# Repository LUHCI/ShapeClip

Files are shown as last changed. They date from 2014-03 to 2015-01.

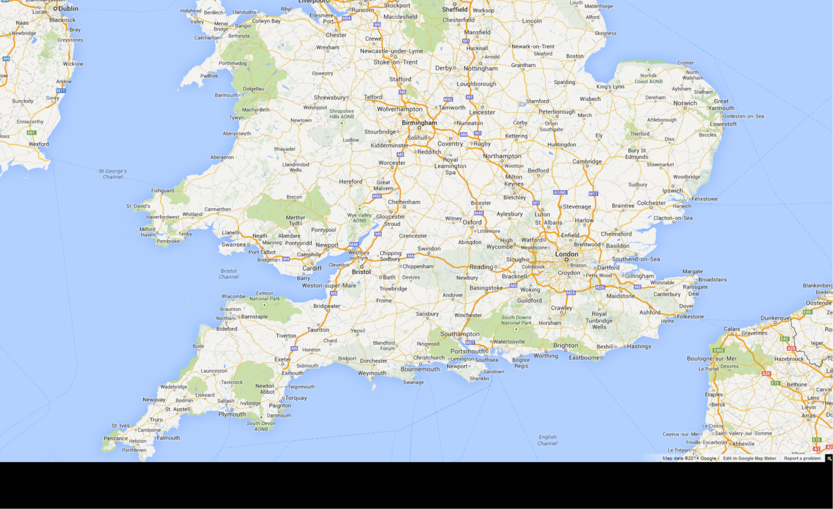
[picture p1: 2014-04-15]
20_Applications/res/uk_map_small.png

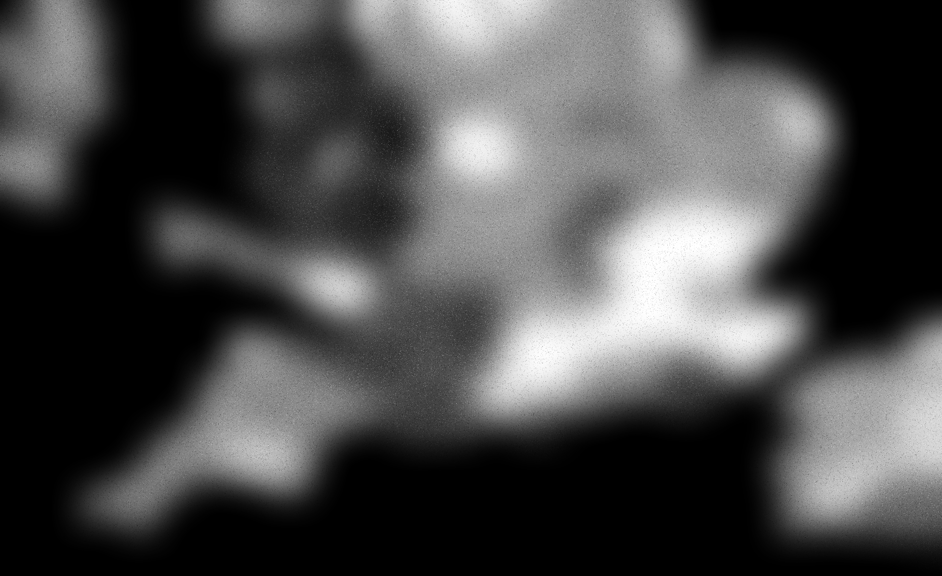
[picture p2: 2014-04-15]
20_Applications/res/uk_population_grayscale.png

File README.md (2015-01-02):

# ShapeClip

## Towards Rapid Prototyping with Shape-Changing Displays for Designers

ShapeClip is a modular tool capable of transforming any computer screen into a z-actuating shape-changing display. This enables designers to produce dynamic physical forms by simply ‘clipping’ actuators onto screens.

ShapeClip displays are portable, scalable, fault-tolerant, and support runtime actuator re-arrangement. Users are not required to have knowledge of electronics or programming, and can develop motion designs with presentation software, image editors, and for those who require more control, web-standard interfaces.

<a href="http://www.youtube.com/watch?feature=player_embedded&v=5YozIqFVEgY
" target="_blank">ShapeClip</a>

## Getting Started

There are 4 main software packages included here:

1. [Clip Firmware](../master/00_Firmware/Firmware/Firmware.ino) + [Servo Extensions](../Slider/00_Firmware/Firmware/Firmware.ino)
2. [Websocket/Serial Bridge](../master/10_Driver/wsserial)
3. [SUR40 Clip Detector (OpenCV)](../master/15_Middleware/ShapeClipDetector)
4. [Javascript API](../master/10_Driver/ShapeClipAPI.js)
5. [Web-based Sample Apps](../master/20_Applications)

In terms of software that can be used to create motion designs, ShapeClip is not restricted to any particular software package. You are free to work with the tools you know.

To get started you will need to get your hands on some ShapeClip hardware.To do that, you can view our design documents in the 01_Hardware folder.

The following image is a trace (from Eagle) of the ShapeClip mkIII board. The different colours denote different layers of the circuit.
ShapeClip mkIII Board

Each standard Clip weighs ≈30g, and is 20×20×80mm when closed, and costs ≈USD$15. The selected stepper motor has 60mm of travel. Under stress, individual Clips draw between 60–540mA at 5V, enabling small groups to be powered via USB. When powering larger numbers, be sure not to make the chain of clips too long as you may damage the Clips. Clips are connected together with pin connectors that double up as a power transmission method. When the Clip is held upright, the top two pins of the power connector are +5v and the bottom one is GND. The motor and circuit logic are kept separate in the top two pins, but in most scenarios they can share power.
ShapeClip mkIII Board

## Research

This work was conducted as part of the GHOST project (http://ghostfet-prod.cs.bris.ac.uk/) to further the understanding of shape-changing computer interfaces.

You can view our paper (CHI2015) online here. To cite the paper, use the following citation: ...

GHOST Logo

## License

Copyright (c) Lancaster University, GHOST Project

Permission is hereby granted, free of charge, to any person obtaining a copy of this software and associated documentation files (the "Software"), to deal in the Software without restriction, including without limitation the rights to use, copy, modify, merge, publish, distribute, sublicense, and/or sell copies of the Software, and to permit persons to whom the Software is furnished to do so, subject to the following conditions:

The above copyright notice and this permission notice shall be included in all copies or substantial portions of the Software.

THE SOFTWARE IS PROVIDED "AS IS", WITHOUT WARRANTY OF ANY KIND, EXPRESS OR IMPLIED, INCLUDING BUT NOT LIMITED TO THE WARRANTIES OF MERCHANTABILITY, FITNESS FOR A PARTICULAR PURPOSE AND NONINFRINGEMENT. IN NO EVENT SHALL THE AUTHORS OR COPYRIGHT HOLDERS BE LIABLE FOR ANY CLAIM, DAMAGES OR OTHER LIABILITY, WHETHER IN AN ACTION OF CONTRACT, TORT OR OTHERWISE, ARISING FROM, OUT OF OR IN CONNECTION WITH THE SOFTWARE OR THE USE OR OTHER DEALINGS IN THE SOFTWARE.

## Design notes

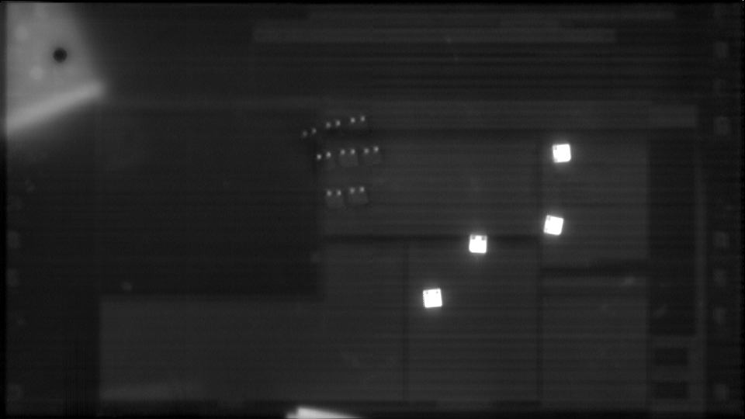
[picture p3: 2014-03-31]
15_Middleware/ShapeClipDetector/ExampleImages/camera635316341878029419.png

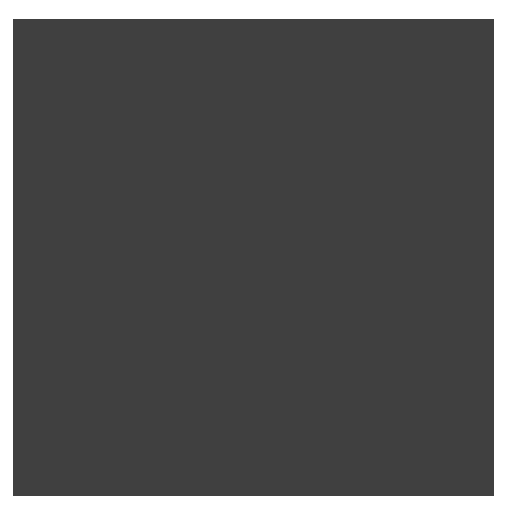
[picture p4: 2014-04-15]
20_Applications/res/lens.png

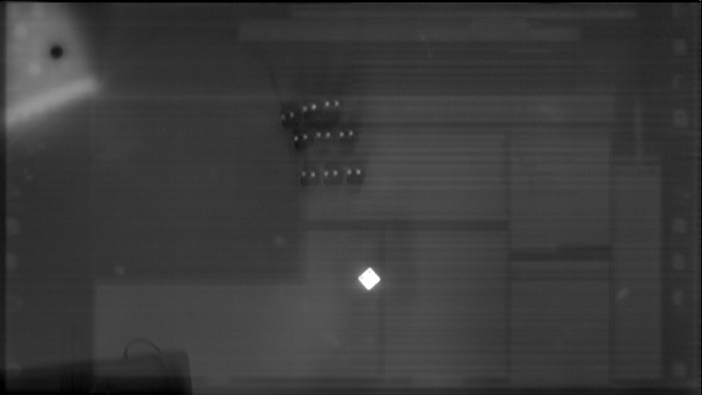
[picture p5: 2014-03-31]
15_Middleware/ShapeClipDetector/ExampleImages/camera635316160988762182.png

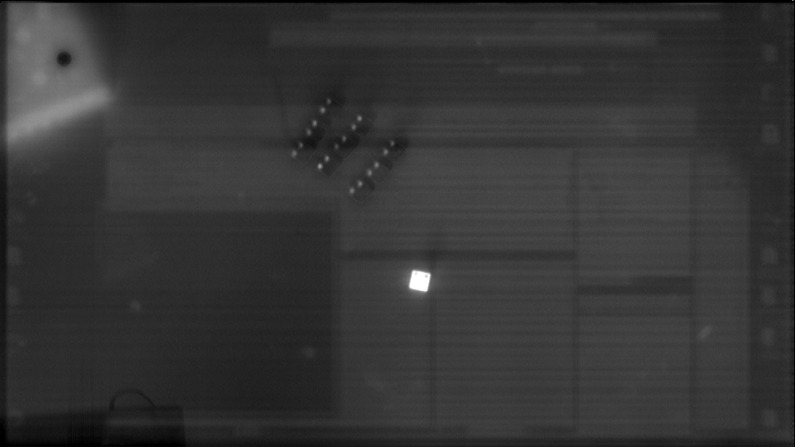
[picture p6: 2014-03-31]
15_Middleware/ShapeClipDetector/ExampleImages/camera635316013497396158.png

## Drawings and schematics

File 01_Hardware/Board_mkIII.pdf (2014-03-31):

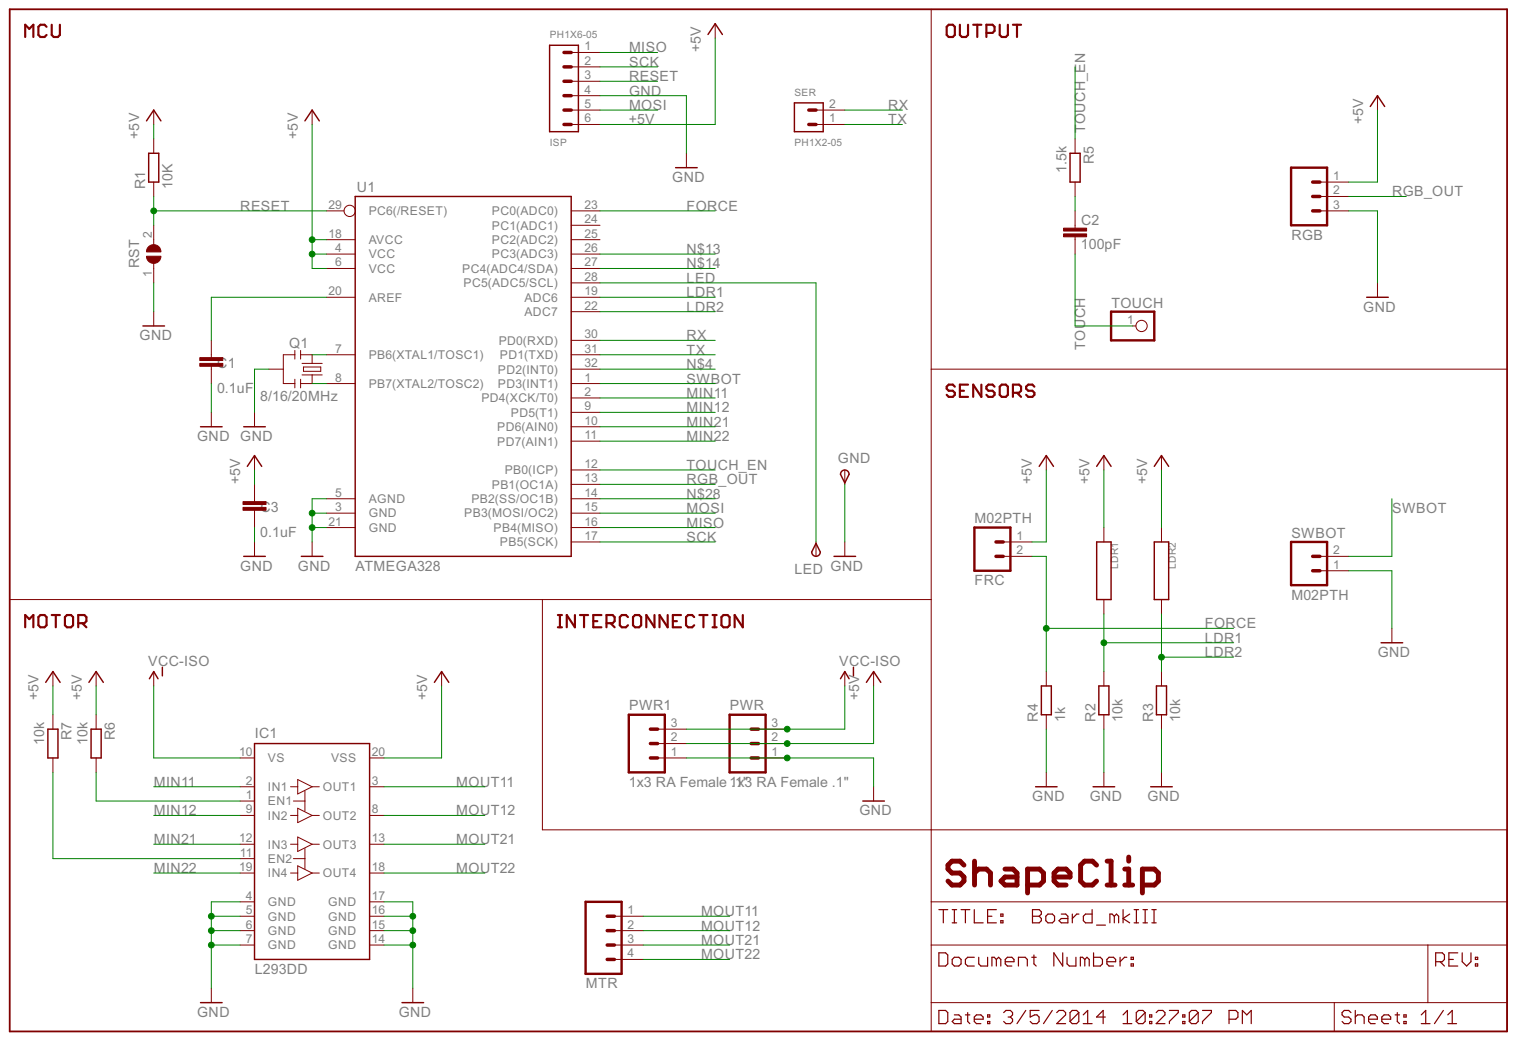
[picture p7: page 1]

VCC-ISO | VCC-ISO

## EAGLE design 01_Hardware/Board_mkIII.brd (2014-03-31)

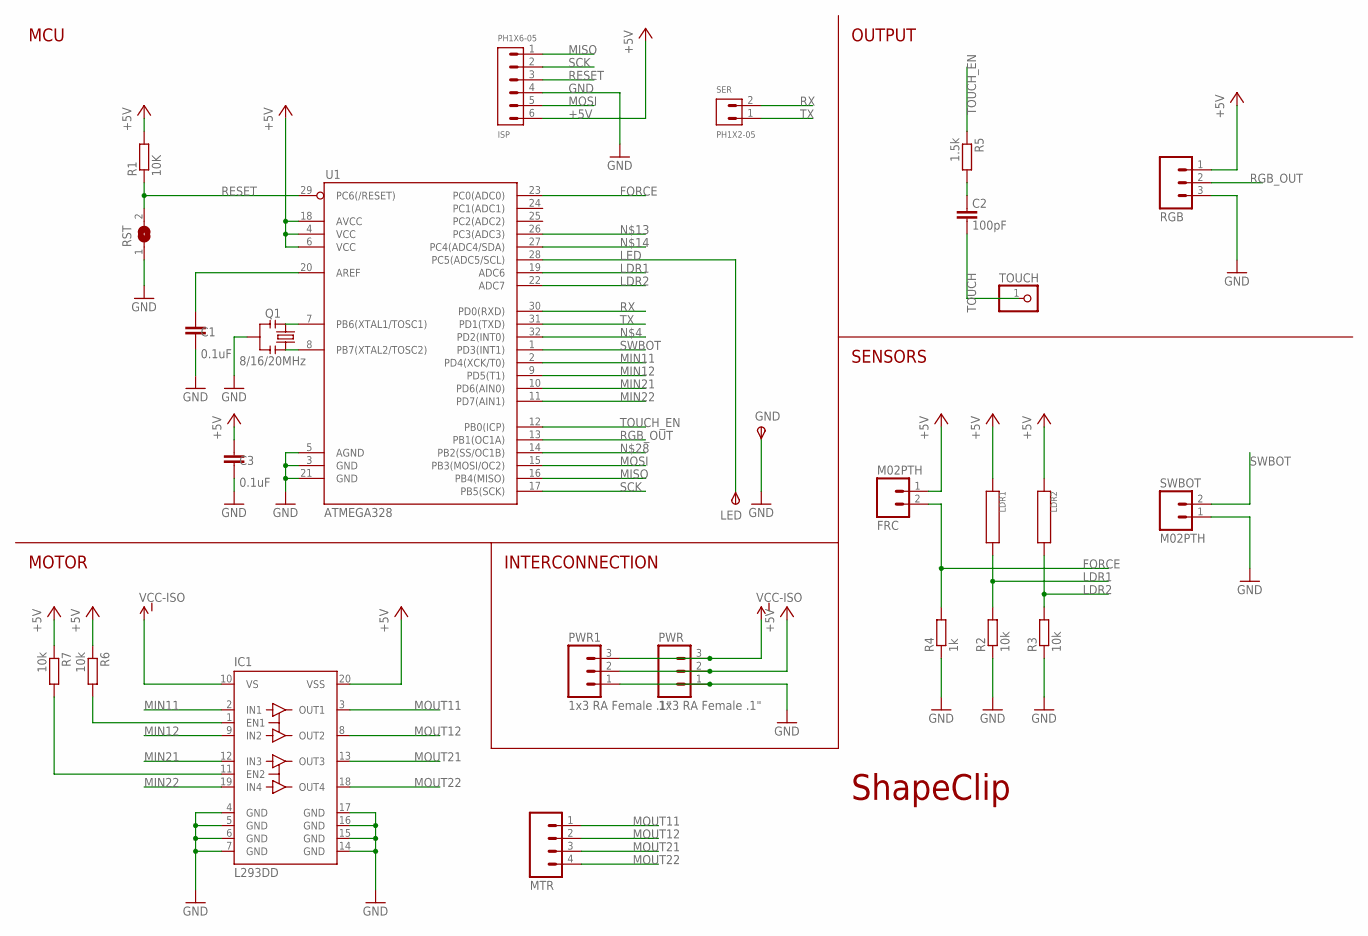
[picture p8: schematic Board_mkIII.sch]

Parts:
C1, C3: 0.1uF; C0603
C2: 100pF; C0603
FRC: M02PTH; 1X02
GND: TPSTP20SQ; TP20SQ
IC1: L293DD; SO20
ISP: PH1X6-05; PH005-1-6
LDR1, LDR2: DR3-31-LDRLONG; DR3-31-LDR_L
LED: TPSTP20SQ; TP20SQ
MTR: M04PTH; 1X04
PWR, PWR1: 1x3 RA Female .1"; PHD_FEMALE_3_90DEG
Q1: 8/16/20MHz; RESONATOR-SMD
R1: 10K; R0603
R2, R3, R6, R7: 10k; R0603
R4: 1k; R0603
R5: 1.5k; R0603
RGB: M03PTH; 1X03
RST: SJW
SER: PH1X2-05; PH005-1-2
SWBOT: M02PTH; 1X02
TOUCH: PINHD-1X1; 1X01
U1: ATMEGA328; TQFP32-08

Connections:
+5V: C3.2, FRC.1, IC1.20 (VSS), ISP.6, LDR1.1, LDR2.1, PWR.2, PWR1.2, R1.2, R6.1, R7.1, RGB.1, U1.4 (VCC), U1.6 (VCC), U1.18 (AVCC)
FORCE: FRC.2, R4.2, U1.23 (PC0(ADC0))
GND: C1.1, C3.1, GND.TP, IC1.4 (GND), IC1.5 (GND), IC1.6 (GND), IC1.7 (GND), IC1.14 (GND), IC1.15 (GND), IC1.16 (GND), IC1.17 (GND), ISP.4, PWR.1, PWR1.1, Q1.2, R2.1, R3.1, R4.1, RGB.3, RST.1, SWBOT.1, U1.3 (GND), U1.5 (AGND), U1.21 (GND)
LDR1: LDR1.2, R2.2, U1.19 (ADC6)
LDR2: LDR2.2, R3.2, U1.22 (ADC7)
LED: LED.TP, U1.28 (PC5(ADC5/SCL))
MIN11: IC1.2 (IN1), U1.2 (PD4(XCK/T0))
MIN12: IC1.9 (IN2), U1.9 (PD5(T1))
MIN21: IC1.12 (IN3), U1.10 (PD6(AIN0))
MIN22: IC1.19 (IN4), U1.11 (PD7(AIN1))
MISO: ISP.1, U1.16 (PB4(MISO))
MOSI: ISP.5, U1.15 (PB3(MOSI/OC2))
MOUT11: IC1.3 (OUT1), MTR.1
MOUT12: IC1.8 (OUT2), MTR.2
MOUT21: IC1.13 (OUT3), MTR.3
MOUT22: IC1.18 (OUT4), MTR.4
unnamed: Q1.1, U1.8 (PB7(XTAL2/TOSC2))
unnamed: Q1.3, U1.7 (PB6(XTAL1/TOSC1))
unnamed: C1.2, U1.20 (AREF)
unnamed: C2.2, R5.2
unnamed: IC1.1 (EN1), R6.2
unnamed: IC1.11 (EN2), R7.2
RESET: ISP.3, R1.1, RST.2, U1.29 (PC6(/RESET))
RGB_OUT: RGB.2, U1.13 (PB1(OC1A))
RX: SER.2, U1.30 (PD0(RXD))
SCK: ISP.2, U1.17 (PB5(SCK))
SWBOT: SWBOT.2, U1.1 (PD3(INT1))
TOUCH: C2.1, TOUCH.1
TOUCH_EN: R5.1, U1.12 (PB0(ICP))
TX: SER.1, U1.31 (PD1(TXD))
VCC-ISO: IC1.10 (VS), PWR.3, PWR1.3

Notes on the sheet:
MCU
MOTOR
SENSORS
OUTPUT
INTERCONNECTION
ShapeClip

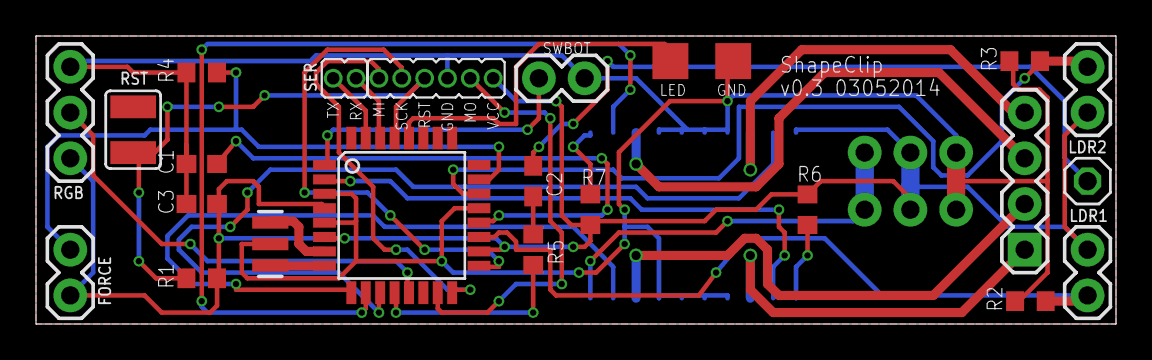
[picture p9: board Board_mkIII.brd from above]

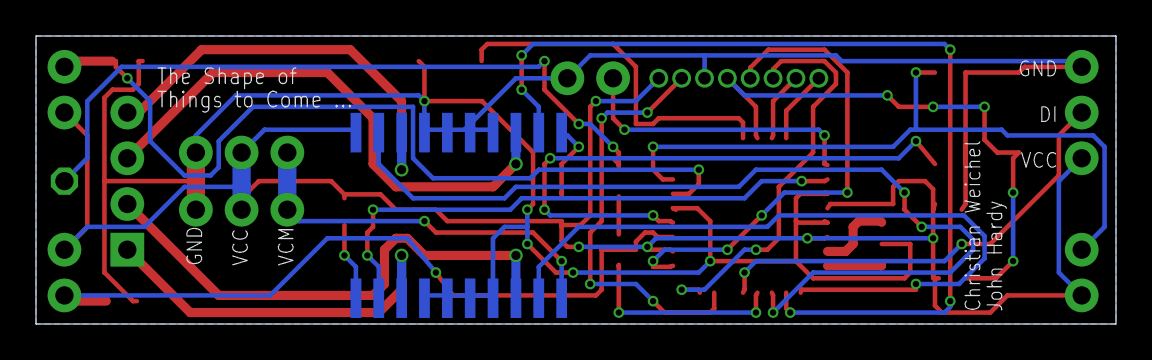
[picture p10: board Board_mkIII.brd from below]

Board: 2 copper layers, 60.0 x 16.0 mm, 27 parts (2 on the bottom side), 31 nets.

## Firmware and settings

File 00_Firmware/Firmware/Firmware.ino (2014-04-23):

/*
	ShapeClip Firmware
	This is logic code used in the ShapeClip paper.
		JH - John Hardy
		CW - Christian Weichel
		JV - John Vidler
		MS - Matthias Schitthelm
	
	v2.5 - JV - Minor tweaks to height mode
	v2.4 - JV - Moved serial buffer updates to a seperate call, serial now updated regardless of mode.	
	v2.3 - JH - Fixes to serial RGB colour display.
	v2.2 - JH - Motor driver accumulator. Known bug which does not let it drive to the extents.
	v2.1 - JH - Bug fixes to the 2.0, added stepper optimisation, decrunchified sync-pulse mode.
	v2.0 - JH - Second version, re-factored and ready for UIST + profiling.
	v1.6 - JV - Updated modes.
	v1.5 - JV - Serial comms added.
	v1.4 - JH - Height mode added.
	v1.3 - JH - Added modes.
	v1.2 - CW - Added LDR.h and LDR.cpp
	v1.1 - CW + MS - Added cool stepper.
	v1.0 - JH - First version, sync-pulse based control of RGB and Height


	/------------------------\
	| SCREEN SERIAL COMMANDS |
 	\------------------------/
        
        Format: [Command][Parameter][X]
        Each part is a single byte, and the last byte should always be ASCII 'X'.
        
        When in serial mode:
        [R][0-255][X] - Set red value
        [G][0-255][X] - Set green value
        [B][0-255][X] - Set blue value
        [H][0-255][X] - Set height value
        [Z][any][X]   - Zero the actuator
        
        When in any mode:
        [M][H][X] - Change to height mode
        [M][Y][X] - Change to syncpulse mode
        [M][S][X] - Change to serial command mode.
        
        
*/

/* External and 3rd party libraries. */ 
#include <Math.h>
#include <EEPROM.h>
#include <util/parity.h>
#include "CoolStepper.h" 
#include "LDR.h"
#include "Adafruit_NeoPixel.h"
#include "WindowVariance.h"

/* IO Pins */
#define PIN_LED   A5		// The on-board LED.
#define PIN_SWTOP 2			// The top switch (digital).
#define PIN_SWBOT 3			// The bottom switch (digital).
#define PIN_FORCE A0		// The force input (analog).
#define PIN_TOUCH 8  		// The touch output (digital).
#define PIN_RGB_OUT 9		// The RGB LED (digital).
#define PIN_MIN11 4			// Motor Coil 1 + (digital).
#define PIN_MIN12 5			// Motor Coil 1 - (digital).
#define PIN_MIN21 6			// Motor Coil 2 + (digital).
#define PIN_MIN22 7			// Motor Coil 2 - (digital).
#define PIN_RND   A4		// Random data source pin.
#define PIN_LDR1  A6		// The LDR1 input (analog).
#define PIN_LDR2  A7		// The LDR2 input (analog).

/* Motor characteristics */
#define MOTOR_ANGLE 20		// The degrees turned with each motor step.
#define MOTOR_SPEED 1500	// The motor speed in rotations per minute (RPMs).
#define MOTOR_TRAVEL 470	// The number of steps to move the nut from the top to the bottom.

/* Sync pulse mode settings. */
const float SYNC_SIGNAL_DROP_THRESHOLD = 3.0f; 				// Based on the behaviour of the LDR with a 10k resistor on a Dell LCD monitor.
const int PULSE_COUNT = 5;									// There are 5 pulses: high, low, r, g, b
const int PULSE_WIDTH = 200;								// The amount of time each pulse last (ms).
const int PULSE_WIDTH_ERR = 10;								// The amount of error in each pulse width start and end (~10ms due to 4ms timers in JS).
const int DATA_WIDTH  = PULSE_WIDTH * PULSE_COUNT;			// The total amount of time for an entire data pulse.
const int DATA_WIDTH_ERR = PULSE_WIDTH_ERR * PULSE_COUNT; 	// The total amount of error for an entire data pulse.
const int SAMPLE_OFFSET = 50;								// The amount of time (ms) to offset the LDR sampling start (relative to the sync drop).
const int SAMPLE_WINDOW = 90;								// The amount of time (ms) to sample the LDR for.

#define PULSE_STATE__NOT_CHECKED  -1	// The sync-pulse routine did not bother checking, too soon since previous check.
#define PULSE_STATE__NO_PULSE      0	// The sync-pulse check returned no pulse.. Probably off a screen.
#define PULSE_STATE__ACTIVE_PULSE  1	// The sync-pulse check returned a pulse! It's probably on a screen.

/** Sensor settings. */
#define ON_SCREEN_TIMEIN 500			// The amount of time before height mode accepts an on screen value. One second in ms.
const int LDR_MIN_LIMIT = 120;				// The smallest acceptable delta between the min and max values of the LDR.
const int LDR_MAX_LIMIT = 1000;				// The largest acceptable delta between the min and max values of the LDR.
#define LDR_OFFSCREEN_DELTA_GAP 100 	// The largest gap between the LDR values at which it is considered off-screen.
#define SSMODE_LDR_SYMB_LOWER -450		// The cap for the lowest LDR symbol.
#define SSMODE_LDR_SYMB_UPPER 500		// The cap for the highest LDR symbol.

/* Application Behaviours */
#define MODE_PROFILING 			// Does the Clip accept basic serial commands: p,s,f (ping, start, finish).
#define PROFILING_RATE 50U		// The rate at which we stream data to serial in profiling mode.
#define SSMODE_8BIT				// Run screen-serial in 8 bit mode (recommended).
//#define SSMODE_16BIT			// Run screen-serial in 16 bit mode (not recommended or tested that much).

/* Serial Debugging modes. */
//#define HEIGHT_DEBUG			// Height mode: Enable serial print of debug messages.
//#define SYNCPULSE_DEBUG		// Sync pulse mode: Enable serial print of debug messages.
//#define SSMODE_CMDPRINT		// Screen serial mode: Enable serial print of command buffer interpretations.
//#define SSMODE_STREAMPRINT	// Screen serial mode: Enable serial print of bitstream data for debugging the serial connection.  <-- this one is cool
//#define SSMODE_TRANSMISSION_GRAPH // Print out the data for the screen-serial transmission graph.
//#define SERIAL_INFO			// Should device values be streamed via serial? csv: ms, ldr1, ldr2, rgb, height, frc, haspulse, swbot
//#define SERIAL_SYNC_DEBUG		// Should sync pulse debug data be streamed via serial? csv: ms, r, g, b
//#define SERIAL_SYNC_DEBUG2	// Should the verbose sync pulse debug data be streamed via serial? csv: ms, slope, max, r, g, b, min, raw
//#define EMIT_MODES

/** Colour modes - how the RGB LED is controlled. */
#define RGBMODE_NONE     0		// The RGB LED displays nothing.
#define RGBMODE_SCREEN   1		// The RGB LED displays the last colour the pulses detected.
#define RGBMODE_NOSCREEN 2		// The RGB LED displays the "not on screen" pattern (i.e. no pulse detected).
#define RGBMODE_STARTUP  3		// The RGB LED displays the "setting up / calibrating" pattern.

/* Colour manipulation macros. */
#define RGB(r,g,b) 	(((r & 0xFF) << 16) | ((g & 0xFF) << 8)  | ((b & 0xFF) << 0))
#define RED(hex) 	hex >> 16 & 0xFF
#define GREEN(hex) 	hex >>  8 & 0xFF
#define BLUE(hex) 	hex >>  0 & 0xFF

/** EEPROM data settings. NOTE: Modes cannot be zero - zero is reserved! */
#define EEMODEADDR 0			// The address of the mode stored in EEPROM.
#define EEMODE_CHANGETIME 5000  // The number of ms to hold the switch before the clip mode is changed.
#define EEMODE_SYNCPULSE  45	// The Clip looks for a sync pulse on one of the LDRs.
#define EEMODE_HEIGHTONLY 37	// The Clip uses both LDRs to estimate height, no colour involved.
#define EEMODE_SERIAL     89	// The Clip can send / recieve serial data with a simple protocol.



/**
 * @brief Check to see if code should be called based on the timer.
 * This can be used to create a rudimentary timer.  It is called once per logic-loop.
 * If it returns true, then the timer handler code should be run.  If false, then it should not.
 * Based on: http://forum.arduino.cc/index.php/topic,5686.0.html
 * Usage: ulong timer = 0; if (cycleCheck(&timer, 10u) { log("called every 10 ms"); }
 * @param *iLastMs Pointer to a value which contains the last time this was checked.
 * @param iCycle The number of ms since the last time required to trigger.
 * @return True if the time since the last call has elasped and the code should run. False if not.
 */
boolean cycleCheck(unsigned long *iLastMs, unsigned int iCycle)  {
	unsigned long ms = millis();
	if(ms - *iLastMs >= iCycle)
	{
		*iLastMs = ms;
		return true;
	}
	else
	{
		return false;
	}
}

/**
 * @brief Reset a timer that is used with the cycleCheck function.
 * @param *iLastMs Pointer to a value which contains the last time this was checked.
 * This will update the iLastMs value to the current time.
 */
void cycleReset(unsigned long *iLastMs) {
	*iLastMs = millis();
}

/**
 * @brief Work out if a time value falls within a sample window. 
 * @param iRelativeTime The time to check.
 * @param iSampleOffset The sampling offset start (relative to 0 in iRelativeTime).
 * @param iWindowSize The sampling window size.
 * @return True if (iSampleOffset+iWindowSize) > iRelativeTime > iSampleOffset.
 */
boolean checkSample(int iRelativeTime, int iSampleOffset, int iWindowSize) {
	return (iRelativeTime > iSampleOffset) && ( iRelativeTime < (iSampleOffset + iWindowSize));
}


// ShapeClip v1 controls and live values.
Stepper motor(MOTOR_ANGLE, PIN_MIN11, PIN_MIN12, PIN_MIN21, PIN_MIN22);
Adafruit_NeoPixel pRGB = Adafruit_NeoPixel(1, PIN_RGB_OUT, NEO_GRB + NEO_KHZ800);
LDR ldr1(PIN_LDR1);
LDR ldr2(PIN_LDR2);

boolean bMotorCalibrated = false;	// Is the motor position value accurate?
int iMotorPosition = 0;				// The current number of steps in the motor.

int eClipMode = EEMODE_SYNCPULSE;	// Current Clip mode.
int eRGBMode = RGBMODE_NONE;		// Current RGB mode.
bool bOnScreen = false;				// Is the shape clip device on the screen (i.e. does it have a valid sync pulse)?

int iTargetR = 0;					// Target RED component.
int iTargetG = 0;					// Target GREEN component.
int iTargetB = 0;					// Target BLUE component.
int iTargetPos = 0;					// Target MOTOR height (steps).



/**
 * @brief Configure the chip pins to the proper states.
 */
void configure() {
	
	// On-board LED (output, off).
	pinMode(PIN_LED, OUTPUT);
	digitalWrite(PIN_LED, LOW);
	
	// LDR1 and LDR2 (input). NOT REQUIRED FOR ANALOG PINS - MAYBE HARMFUL
	//pinMode(PIN_LDR1, INPUT);
	//pinMode(PIN_LDR2, INPUT);
	
	// Top and bottom switches (input, active).
	pinMode(PIN_SWTOP, INPUT);
	digitalWrite(PIN_SWTOP, HIGH);
	pinMode(PIN_SWBOT, INPUT);
	digitalWrite(PIN_SWBOT, HIGH);
	
	// Touch sensor (output, low).
	pinMode(PIN_TOUCH, OUTPUT);
	digitalWrite(PIN_TOUCH, LOW);
	
	// Force sensor (input).
	pinMode(PIN_FORCE, INPUT);
	
	// Set up the motor.
	motor.setSpeed(MOTOR_SPEED);
	
	// Set up the RGB LED.
	pRGB.begin();
	pRGB.show();
	
	// On-board LED (on).
	digitalWrite(PIN_LED, HIGH);
}

/**
 * @brief This will send the motor DOWN until the SWBOT is triggered OR the full MOTOR_TRAVEL is used.
 * It will set the iMotorPosition value to 0 and not allow calls to moveMotor while operating.
 */
void zeroMotor() {
	
	// Zero flags.
	bMotorCalibrated = false;
	
	// Put us into setup mode (RGB LED).
	int eLastMode = eRGBMode;
	eRGBMode = RGBMODE_STARTUP;
	updateColour();
	
	// Until the motor is calibrated, step down each time.
	for(int iAvailableSteps = MOTOR_TRAVEL; iAvailableSteps >= 0; iAvailableSteps--) {
		motor.step(-1);

		//#ifdef SWBOT_MOTOR
		//if (digitalRead(PIN_SWBOT) == LOW) break;
		//#endif
	}
	
	// Set the motor position to 0 (known location).
	bMotorCalibrated = true;
	iMotorPosition = 0;
	
	// Shut the motor down.
	motor.shutdown();
	
	// Take us out of setup mode.
	eRGBMode = eLastMode;
	updateColour();
}


/**
 * @brief Move the motor one step towards the target position.
 * TODO: There is currently an edge case where we cannot drive the motor all the way to the top.
 */
void moveMotor() {
	
	// Only do this if the motor is calibrated.
	if (!bMotorCalibrated)
		return;
	
	#define STEP_ACCM_SIZE 5								// The max number of steps to accumulate before batching.
	static boolean bAllowMotorShutdown = true;				// Is the motor allowed to shutdown.
	static unsigned long shutdownTimeout = millis();		// The time of the last step.
	static unsigned int iStepAccumulator = 0;				// The step accumulator.
	
	
	// If we have a small change in position, add it to the accumulator.
	//   so that we can batch it later.  If we do not do this, small steps
	//   are often lost.
	//   This also has the nice side effect as acting like a noise absorber.
	int iDelta = iTargetPos - iMotorPosition;
	if (abs(iDelta) < STEP_ACCM_SIZE)
	{
		iStepAccumulator += iDelta;
		iDelta = 0;
	}
	
	// If the accumulated steps + the change this frame is over the minimum step, then step.
	int iAdjustedSteps = iStepAccumulator + iDelta;
	
	// Or if we are at either end (the accumulator would absorb it, so we need a (literal) edge case).
	//bool bEdgeCase = ((iTargetPos < (0 + STEP_ACCM_SIZE)) || (iTargetPos > (MOTOR_TRAVEL - STEP_ACCM_SIZE)) & abs(iAdjustedSteps) > 2) ;
	
	// Do the check.
	if (abs(iAdjustedSteps) >= STEP_ACCM_SIZE /* || bEdgeCase */) 
	{
		// Compute the step direction.
		int step = iAdjustedSteps >= 0 ? 1 : -1;
		
		/* vv This approach leads to jumpy / inconsistent step behaviours.
		// Limit to 25 steps per frame.
		if (abs(iAdjustedSteps) <= 25)
		{
			motor.step(step * iAdjustedSteps);
			iMotorPosition += (step * iAdjustedSteps);
		}
		else
		{
			motor.step(step * 25);
			iMotorPosition += (step * 25);
		}
		*/
		
		/* vv This approach leads to faster and smoother stepping, kinda tearing noisy tho. */
		if (abs(iAdjustedSteps) > 20)
		{
			motor.step(step * 20);
			iMotorPosition += (step * 20);
		}
		if (abs(iAdjustedSteps) > 10)
		{
			motor.step(step * 10);
			iMotorPosition += (step * 10);
		}
		else
		{
			motor.step(step);
			iMotorPosition += step;
		}
		
		//Serial.print("Stepping ");
		//Serial.println(iAdjustedSteps);
		
		// Write the last step time.
		shutdownTimeout = millis();
		bAllowMotorShutdown = true;
	}
	
	// If we have not stepped for 0.5s, turn off the motor.
	if ((millis() - shutdownTimeout) > 250)
	{
		// If we have not already shut the motor down.
		//if (bAllowMotorShutdown)
		//{
			motor.shutdown();
			bAllowMotorShutdown = false;
		//}
	}
	
	
	
	
	/*
	// Compute the distance to travel.
	int iDelta = iTargetPos - iMotorPosition;
	
	// If we have to move over 2 steps in either direction.
	if (abs(iDelta) > 1)
	{
		// Move one step in the correct direction and update the motor position.
		int step = iDelta >= 0 ? 1 : -1;
		
		// Skip for 20 steps.
		if (abs(iDelta) > 20)
		{
			motor.step(step * 20);
			iMotorPosition += (step * 20);
		}
		// Skip for 10 steps.
		if (abs(iDelta) > 10)
		{
			motor.step(step * 10);
			iMotorPosition += (step * 10);
		}
		// Detailed steps.
		else
		{
			motor.step(step);
			iMotorPosition += step;
		}
	}
	
	// Otherwise shut the motor down.
	else
	{
		motor.shutdown();
	}
	*/
}

/**
 * @brief Display the correct colour on the RGB led based on the mode it is in.
 */
void updateColour() {
	
	// If we are in the normal mode.
	switch (eRGBMode)
	{
		case RGBMODE_NONE:
			pRGB.setPixelColor(0,  0, 0, 0);
			break;
		case RGBMODE_SCREEN:
			{
				// Go immediately to the new colour.
				// pRGB.setPixelColor(0,  iTargetR, iTargetG, iTargetB);
				
				// Get 1% closer to the target colour each iteration.
				uint32_t currentColor = pRGB.getPixelColor(0);
				int stepRed   = constrain(map(10, 0, 1000, RED(currentColor),   iTargetR), 0, iTargetR);
				int stepGreen = constrain(map(10, 0, 1000, GREEN(currentColor), iTargetG), 0, iTargetG);
				int stepBlue  = constrain(map(10, 0, 1000, BLUE(currentColor),  iTargetB), 0, iTargetB);
				
				// Set the step value.
				pRGB.setPixelColor(0,  stepRed, stepGreen, stepBlue);
			}
			break;
		case RGBMODE_NOSCREEN:
			pRGB.setPixelColor(0,  255, 0, 0);
			break;
		case RGBMODE_STARTUP:
			if (eClipMode == EEMODE_HEIGHTONLY)
				pRGB.setPixelColor(0,  255, 0, 0);
			else if (eClipMode == EEMODE_SYNCPULSE)
				pRGB.setPixelColor(0,  0, 255, 0);
			else
				pRGB.setPixelColor(0,  0, 0, 255);
			break;
	}
	
	// Push the new colour.
	pRGB.show();
}




/**
 * Setup the board and configure the pins.
 */
void setup() { 
	
	// Configure the board and pins.
	configure();
	
	// Start the serial port.
	Serial.begin(115200);
	
	// Wait two seconds.
	Serial.println("Boot v2.5");
	
	// Select a default clip mode from the set of possible modes, if one is not set.
	eClipMode = EEPROM.read(EEMODEADDR);
	switch( eClipMode )
	{
	  case EEMODE_SYNCPULSE:
		break;
	  case EEMODE_HEIGHTONLY:
		break;
	  case EEMODE_SERIAL:
		break;
	  default:
		eClipMode = EEMODE_HEIGHTONLY;
		EEPROM.write(EEMODEADDR, EEMODE_HEIGHTONLY);
	}

	// Debug Mode
	//eClipMode = EEMODE_SYNCPULSE;
	//eRGBMode  = RGBMODE_SCREEN;
	detectAndSetModeChange( -1 );   // -1 == set nothing, blink code; 0 = set nothing, wait for button; >0 == set mode to supplied mode

	// Wait for a random time so that not all clips zero their motor at the same time.
	randomSeed(analogRead(PIN_RND));
	uint16_t randomWait = random(1000);
	delay(randomWait);
	
	// Bring the motor down until it hits the bottom.
	zeroMotor();
	
	// make sure we all start at the same time
	delay(1000 - randomWait);
}
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
void loop() {
	
	// Listen for a change in mode.
	detectAndSetModeChange( 0 );

	// Attempt to read a serial bit from the screen.
	screenSerialRead();
	if( cmdBuffer[0] == 'M' && cmdBuffer[2] == 'X' )
	{
		switch( cmdBuffer[1] )
		{
			case 'H': detectAndSetModeChange( EEMODE_HEIGHTONLY ); break;
			case 'Y': detectAndSetModeChange( EEMODE_SYNCPULSE ); break;
			case 'S': detectAndSetModeChange( EEMODE_SERIAL ); break;
		}
		cmdBuffer[0] = 0;
		cmdBuffer[1] = 0;
		cmdBuffer[2] = 0;
	}
	
	// Detect which mode we are in.
	switch (eClipMode)
	{
		// If we are in EEMODE_HEIGHTONLY mode, just use both LDRs for height.
		case EEMODE_HEIGHTONLY:
			loopHeightMode();
			break;
			
		// If we are in EEMODE_SYNCPULSE mode, use the height and colour.
		case EEMODE_SYNCPULSE:
			loopSyncPulseMode();
			break;
			
		// If we are in EEMODE_SERIAL, use the simple binary protocol.
		case EEMODE_SERIAL:
			loopSerialMode();
			break;
			
		// Unknown mode.. should not get here.
		default:
			break;
	}
	
	// If we are in profiling mode.
	#ifdef MODE_PROFILING
	
	static bool bMeasuring = false;			// Are we measuring.
	static unsigned int iMeasureCount = 0;	// How many have we measured.
	
	// Process new commands.
	if (Serial.available())
	{
		byte data = Serial.read();
		switch (data)
		{
			case 'p':	// PING / PONG
				Serial.println("pong");
				break;
			case 'i':	// INFORMATION
				{
					Serial.print(millis()); Serial.print(","); 				// ShapeClip time in ms.
					Serial.print(analogRead(PIN_FORCE)); Serial.print(","); // Force reading.
					Serial.print(iMotorPosition); Serial.print(","); 		// Current MOTOR HEIGHT.
					Serial.print(iTargetPos); Serial.print(","); 			// Target MOTOR HEIGHT.
					Serial.print(iTargetR); Serial.print(","); 				// Target RED
					Serial.print(iTargetG); Serial.print(","); 				// Target GREEN
					Serial.print(iTargetB); Serial.print("\n"); 			// Target BLUE.
				}
				break;
			case 's':	// START STREAMING
				Serial.print("start "); 
				Serial.println(iMeasureCount);
				bMeasuring = true;
				break;
			case 'f':	// FINISH STREAMING
				Serial.print("stop ");
				Serial.println(iMeasureCount);
				bMeasuring = false;
				iMeasureCount ++;
				break;
			case 'z':	// ZERO MOTOR
				zeroMotor();
				break;
		}
	}
	
	// Print out if measuring.
	if (bMeasuring)
	{
		// Rate limit the output stream.
		static unsigned long tmrSample = 0;
		if (cycleCheck(&tmrSample, PROFILING_RATE))
		{
			Serial.print(iMotorPosition); Serial.print(","); 	// Current MOTOR HEIGHT.
			Serial.print(iTargetPos); Serial.print(","); 		// Target MOTOR HEIGHT.
			Serial.print(iTargetR); Serial.print(","); 			// Target RED
			Serial.print(iTargetG); Serial.print(","); 			// Target GREEN
			Serial.print(iTargetB); Serial.print("\n"); 		// Target BLUE.
			
			//#define HRGB(h,r,g,b) 	(((h & 0xFF) << 24) | ((r & 0xFF) << 16) | ((g & 0xFF) << 8)  | ((b & 0xFF) << 0))
			//Serial.println(HRGB(iTargetPos, iTargetR, iTargetG, iTargetB), HEX); // Target HRGB.
		}
	}
	#endif
	
}

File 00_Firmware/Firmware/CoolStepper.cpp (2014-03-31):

/*
  Stepper.cpp - - Stepper library for Wiring/Arduino - Version 0.4
  
  Original library     (0.1) by Tom Igoe.
  Two-wire modifications   (0.2) by Sebastian Gassner
  Combination version   (0.3) by Tom Igoe and David Mellis
  Bug fix for four-wire   (0.4) by Tom Igoe, bug fix from Noah Shibley  
  Shutdown fix           (0.5) by Christian Weichel, Matthias Schittenhelm

  Drives a unipolar or bipolar stepper motor using  2 wires or 4 wires

  When wiring multiple stepper motors to a microcontroller,
  you quickly run out of output pins, with each motor requiring 4 connections. 

  By making use of the fact that at any time two of the four motor
  coils are the inverse  of the other two, the number of
  control connections can be reduced from 4 to 2. 

  A slightly modified circuit around a Darlington transistor array or an L293 H-bridge
  connects to only 2 microcontroler pins, inverts the signals received,
  and delivers the 4 (2 plus 2 inverted ones) output signals required
  for driving a stepper motor.

  The sequence of control signals for 4 control wires is as follows:

  Step C0 C1 C2 C3
	 1  1  0  1  0
	 2  0  1  1  0
	 3  0  1  0  1
	 4  1  0  0  1

  The sequence of controls signals for 2 control wires is as follows
  (columns C1 and C2 from above):

  Step C0 C1
	 1  0  1
	 2  1  1
	 3  1  0
	 4  0  0

  The circuits can be found at 
 
http://www.arduino.cc/en/Tutorial/Stepper
 
 
 */


#include "Arduino.h"
#include "CoolStepper.h"

/*
 * two-wire constructor.
 * Sets which wires should control the motor.
 */
Stepper::Stepper(int number_of_steps, int motor_pin_1, int motor_pin_2)
{
  this->step_number = 0;      // which step the motor is on
  this->speed = 0;        // the motor speed, in revolutions per minute
  this->direction = 0;      // motor direction
  this->last_step_time = 0;    // time stamp in ms of the last step taken
  this->number_of_steps = number_of_steps;    // total number of steps for this motor
  
  // Arduino pins for the motor control connection:
  this->motor_pin_1 = motor_pin_1;
  this->motor_pin_2 = motor_pin_2;

  // setup the pins on the microcontroller:
  pinMode(this->motor_pin_1, OUTPUT);
  pinMode(this->motor_pin_2, OUTPUT);
  
  // When there are only 2 pins, set the other two to 0:
  this->motor_pin_3 = 0;
  this->motor_pin_4 = 0;
  
  // pin_count is used by the stepMotor() method:
  this->pin_count = 2;
}


/*
 *   constructor for four-pin version
 *   Sets which wires should control the motor.
 */

Stepper::Stepper(int number_of_steps, int motor_pin_1, int motor_pin_2, int motor_pin_3, int motor_pin_4)
{
  this->step_number = 0;      // which step the motor is on
  this->speed = 0;        // the motor speed, in revolutions per minute
  this->direction = 0;      // motor direction
  this->last_step_time = 0;    // time stamp in ms of the last step taken
  this->number_of_steps = number_of_steps;    // total number of steps for this motor
  
  // Arduino pins for the motor control connection:
  this->motor_pin_1 = motor_pin_1;
  this->motor_pin_2 = motor_pin_2;
  this->motor_pin_3 = motor_pin_3;
  this->motor_pin_4 = motor_pin_4;

  // setup the pins on the microcontroller:
  pinMode(this->motor_pin_1, OUTPUT);
  pinMode(this->motor_pin_2, OUTPUT);
  pinMode(this->motor_pin_3, OUTPUT);
  pinMode(this->motor_pin_4, OUTPUT);

  // pin_count is used by the stepMotor() method:  
  this->pin_count = 4;  
}

/*
  Sets the speed in revs per minute

*/
void Stepper::setSpeed(long whatSpeed)
{
  this->step_delay = 60L * 1000L / this->number_of_steps / whatSpeed;
}

/*
  Moves the motor steps_to_move steps.  If the number is negative, 
   the motor moves in the reverse direction.
 */
void Stepper::step(int steps_to_move)
{  
	int steps_left = abs(steps_to_move);  // how many steps to take
  
	// determine direction based on whether steps_to_mode is + or -:
	if (steps_to_move > 0) this->direction = 1;
	if (steps_to_move < 0) this->direction = 0;
	
	
	// decrement the number of steps, moving one step each time:
	while(steps_left > 0) {
		// move only if the appropriate delay has passed:
		if (millis() - this->last_step_time >= this->step_delay) {
			this->last_step_time = millis();

			if(steps_left > 0) {
				// increment or decrement the step number,
				// depending on direction:
				if (this->direction == 1) {
					this->step_number++;
					if (this->step_number == this->number_of_steps) {
						this->step_number = 0;
					}
				} else { 
					if (this->step_number == 0) {
						this->step_number = this->number_of_steps;
					}
					this->step_number--;
				}
				
				// step the motor to step number 0, 1, 2, or 3:
				stepMotor(this->step_number % 4);
			} else {
				//this->shutdown();
			}

			steps_left--;
		}
	}
}

void Stepper::shutdown()
{
	if (this->pin_count == 2) {
		digitalWrite(motor_pin_1, LOW);
		digitalWrite(motor_pin_2, LOW);
	} else if (this->pin_count == 4) {
		digitalWrite(motor_pin_1, LOW);
		digitalWrite(motor_pin_2, LOW);
		digitalWrite(motor_pin_3, LOW);
		digitalWrite(motor_pin_4, LOW); 
	}
}

/*
 * Moves the motor forward or backwards.
 */
void Stepper::stepMotor(int thisStep)
{
  if (this->pin_count == 2) {
	switch (thisStep) {
	  case 0: /* 01 */
	  digitalWrite(motor_pin_1, LOW);
	  digitalWrite(motor_pin_2, HIGH);
	  break;
	  case 1: /* 11 */
	  digitalWrite(motor_pin_1, HIGH);
	  digitalWrite(motor_pin_2, HIGH);
	  break;
	  case 2: /* 10 */
	  digitalWrite(motor_pin_1, HIGH);
	  digitalWrite(motor_pin_2, LOW);
	  break;
	  case 3: /* 00 */
	  digitalWrite(motor_pin_1, LOW);
	  digitalWrite(motor_pin_2, LOW);
	  break;
	} 
  }
  if (this->pin_count == 4) {
	switch (thisStep) {
	  case 0:    // 1010
	  digitalWrite(motor_pin_1, HIGH);
	  digitalWrite(motor_pin_2, LOW);
	  digitalWrite(motor_pin_3, HIGH);
	  digitalWrite(motor_pin_4, LOW);
	  break;
	  case 1:    // 0110
	  digitalWrite(motor_pin_1, LOW);
	  digitalWrite(motor_pin_2, HIGH);
	  digitalWrite(motor_pin_3, HIGH);
	  digitalWrite(motor_pin_4, LOW);
	  break;
	  case 2:    //0101
	  digitalWrite(motor_pin_1, LOW);
	  digitalWrite(motor_pin_2, HIGH);
	  digitalWrite(motor_pin_3, LOW);
	  digitalWrite(motor_pin_4, HIGH);
	  break;
	  case 3:    //1001
	  digitalWrite(motor_pin_1, HIGH);
	  digitalWrite(motor_pin_2, LOW);
	  digitalWrite(motor_pin_3, LOW);
	  digitalWrite(motor_pin_4, HIGH);
	  break;
	} 
  }
}

/*
  version() returns the version of the library:
*/
int Stepper::version(void)
{
  return 4;
}

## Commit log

2014-03-31 Added the hardware
    So far only the schematics and board
    [Board_mkIII.brd, Board_mkIII.sch]
2014-03-31 Motor now shutdowns correctly - makes it smooth like butter
    [CoolStepper.cpp, Firmware.ino]
2014-04-01 Common Driver Code
    Pulled out the driver code and got the examples pulled out too.
2014-04-09 FW- Height mode FW- Interpolation FW- Motor Shutdown Driver- Height Mode Driver- Apps Folder FW- Motor accuracy improvement
2014-04-10 driver matches faster comms
2014-04-10 Web Socket Serial Bridge, Profiling Firmware Mode
    Also added the pack and unpack stuff to the test driver and upgraded all
    the parts to set new target values.
2014-04-12 Fixed serial bugs, changed diff drive state interpreter, begun upgrading API.
    [Firmware.ino]
2014-04-12 Firmware v2.2 Motor Accumulator
2014-04-12 Added agressive motor cooling patch
    Keeping at 2.2 (since all clips upgraded)
2014-04-12 v2.3 Fixed serial RGB display... whoops
    [Firmware.ino]
2014-04-13 Longer sample frames
2014-04-14 Slower but better quality sample
2014-04-14 Reduced sample times
2014-04-14 Sample resolution incrase

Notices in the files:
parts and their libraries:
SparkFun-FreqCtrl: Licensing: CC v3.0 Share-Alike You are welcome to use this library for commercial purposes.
